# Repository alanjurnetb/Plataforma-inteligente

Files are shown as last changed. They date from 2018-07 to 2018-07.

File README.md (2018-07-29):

# Plataforma-inteligente
<h1>PLATAFORMA INTELIGENTE PARA DESARROLLO DE VEHÍCULOS MÓVILES AUTÓNOMOS</h1>

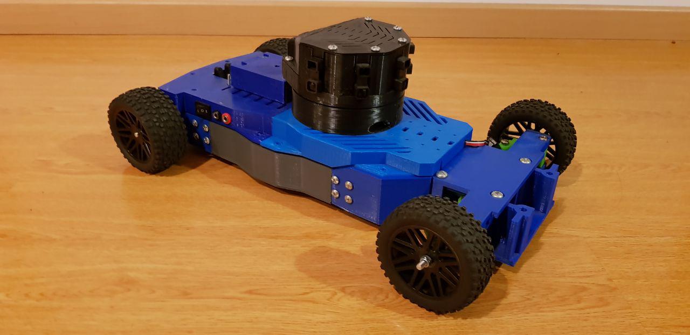
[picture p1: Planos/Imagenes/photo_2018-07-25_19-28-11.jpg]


<h2>Fabricación:</h2>
<h3>Mecánica</h3>

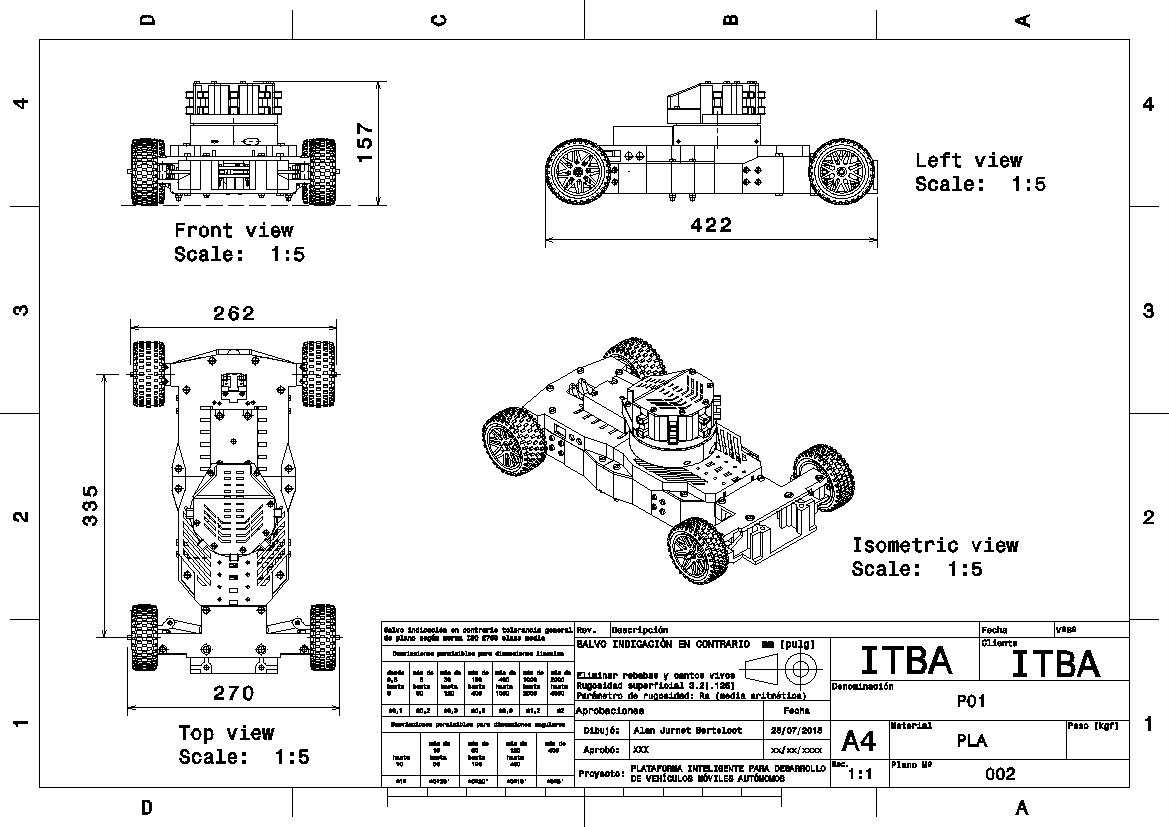
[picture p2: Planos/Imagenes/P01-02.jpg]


Todos los planos y los componentes estan detallados en la carpeta correspondiente.
A continuacion se muestra como es el ensamble y cuales son las piezas que deben utilziarse.
Todas las piezas impresas tienen una codificacion en el nombre que indica como se recomienda que sean impresas.

<b>XXXX-XXXX-I3D-L04-W20-IF50</b>

Esto indica que es una pieza impresa en 3D con capa de 0.4 mm pared de 2 mm y relleno de 50%.

<h4>Tracción</h4>

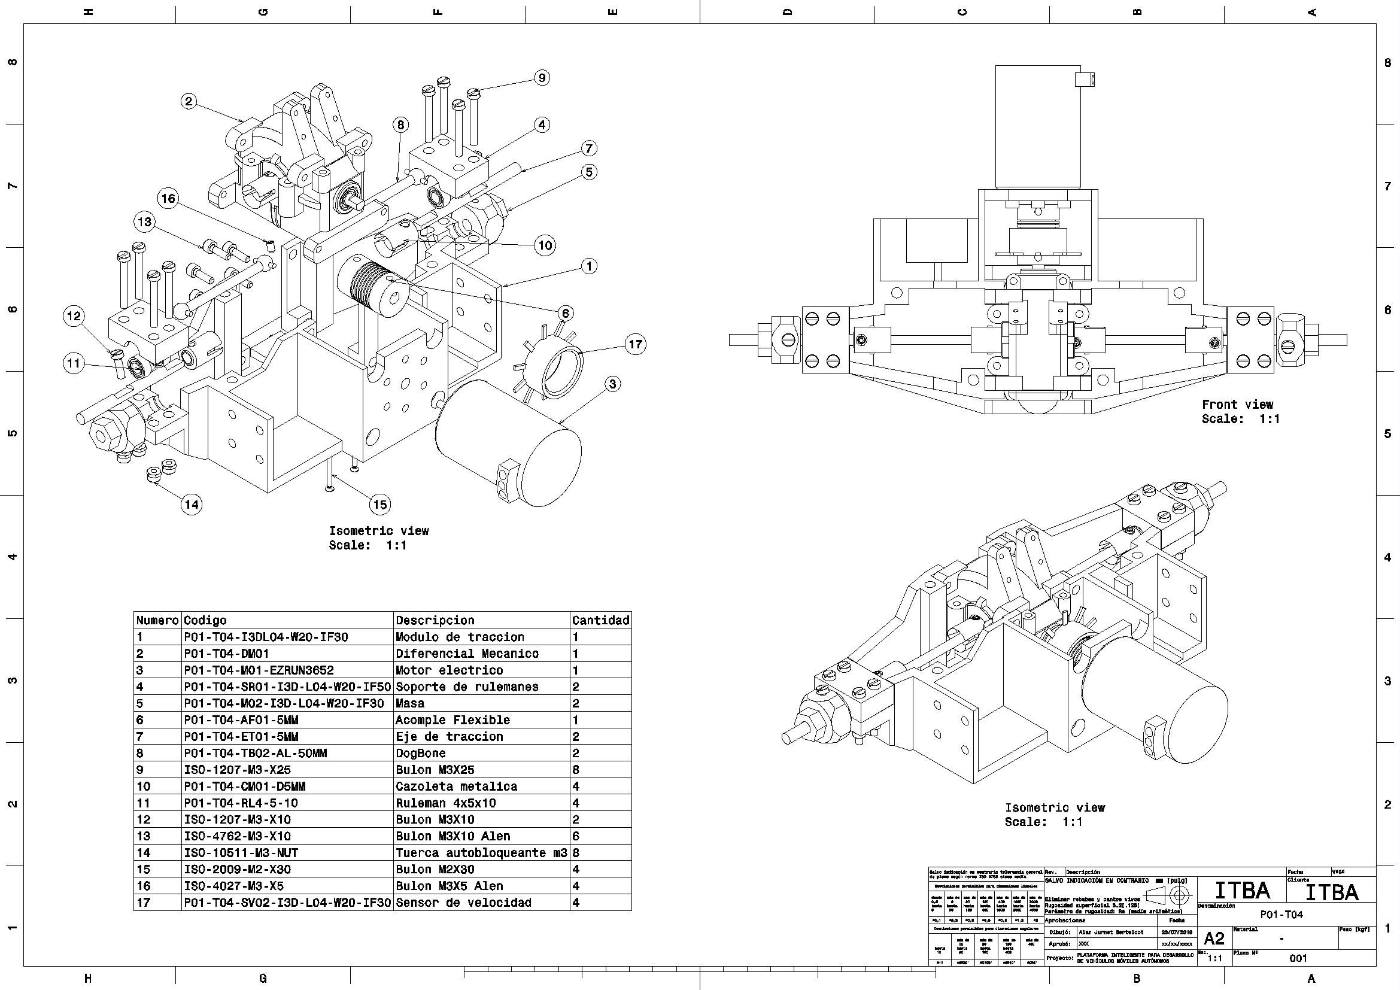
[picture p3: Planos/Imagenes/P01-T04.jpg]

<h4>Dirección</h4>

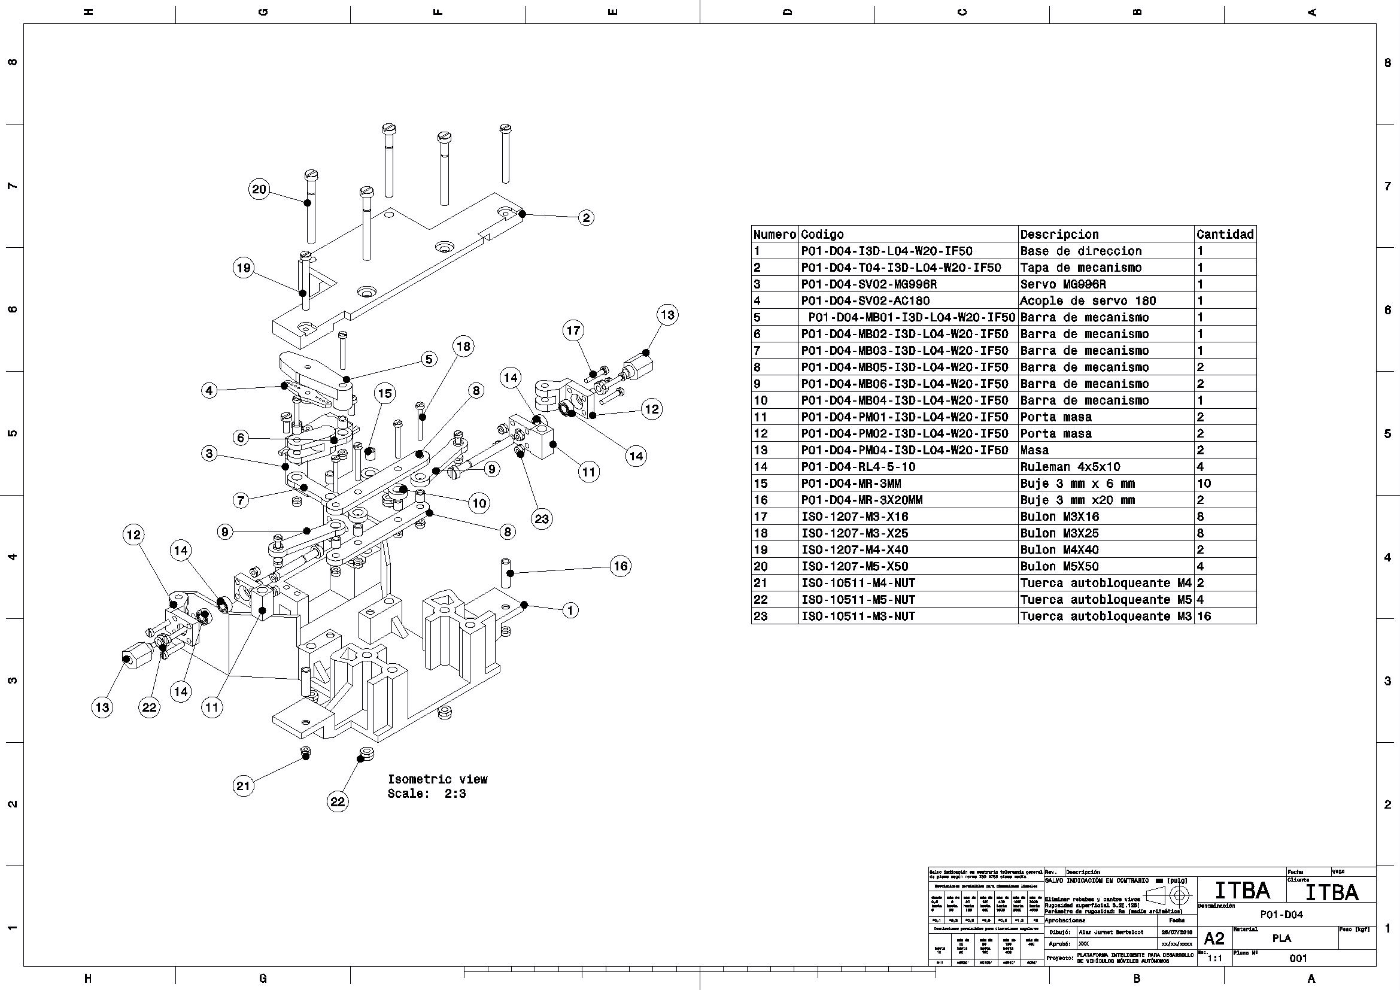
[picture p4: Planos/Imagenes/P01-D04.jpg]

<h4>Chasis</h4>

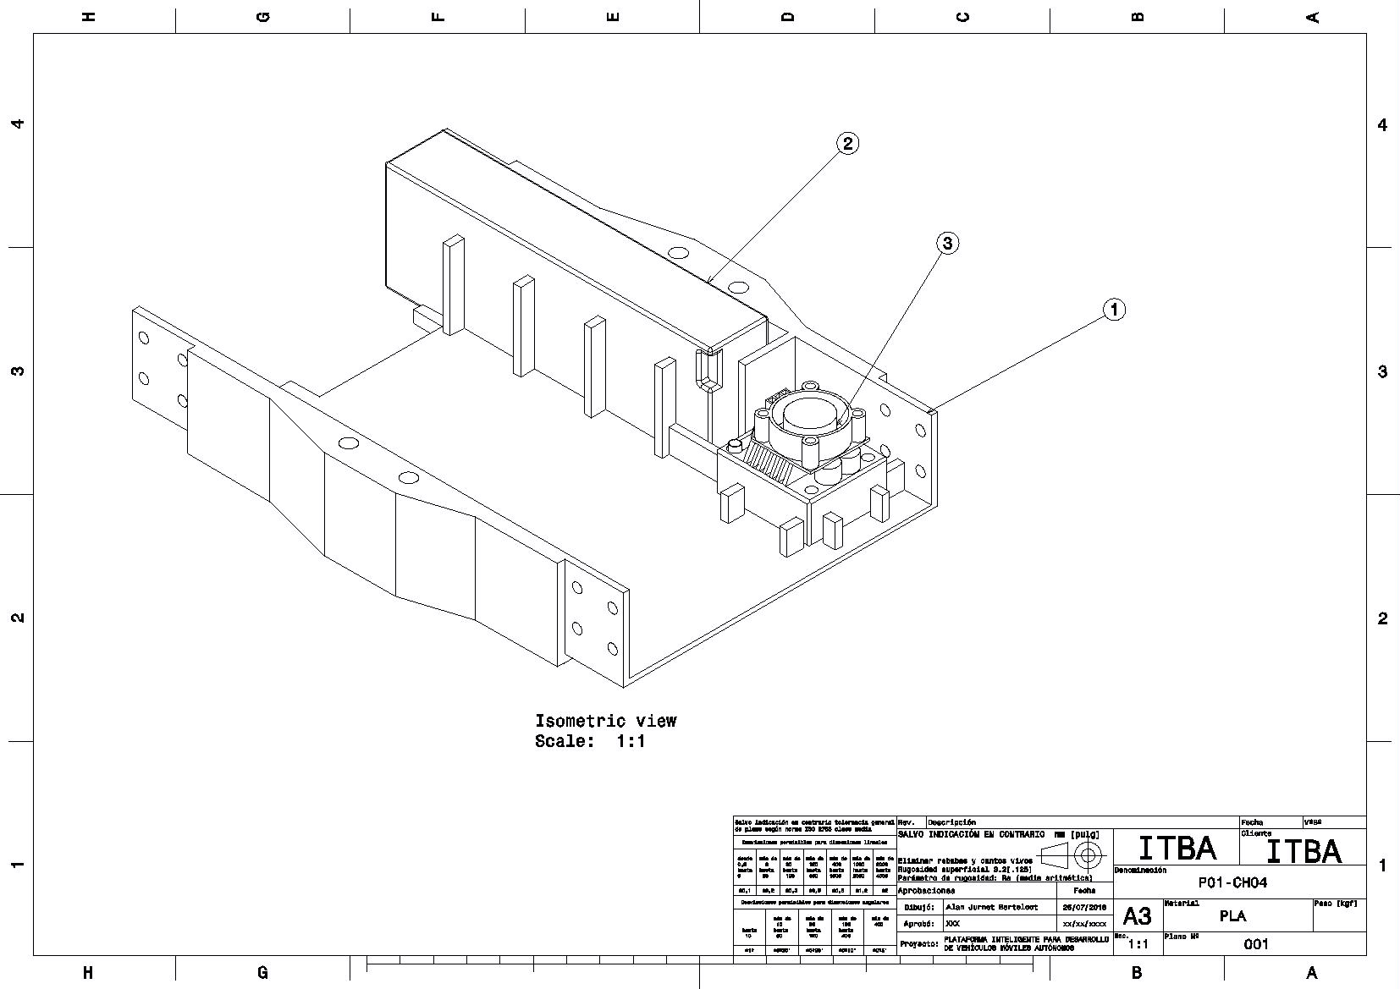
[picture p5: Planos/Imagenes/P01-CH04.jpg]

<h4>Radar</h4>

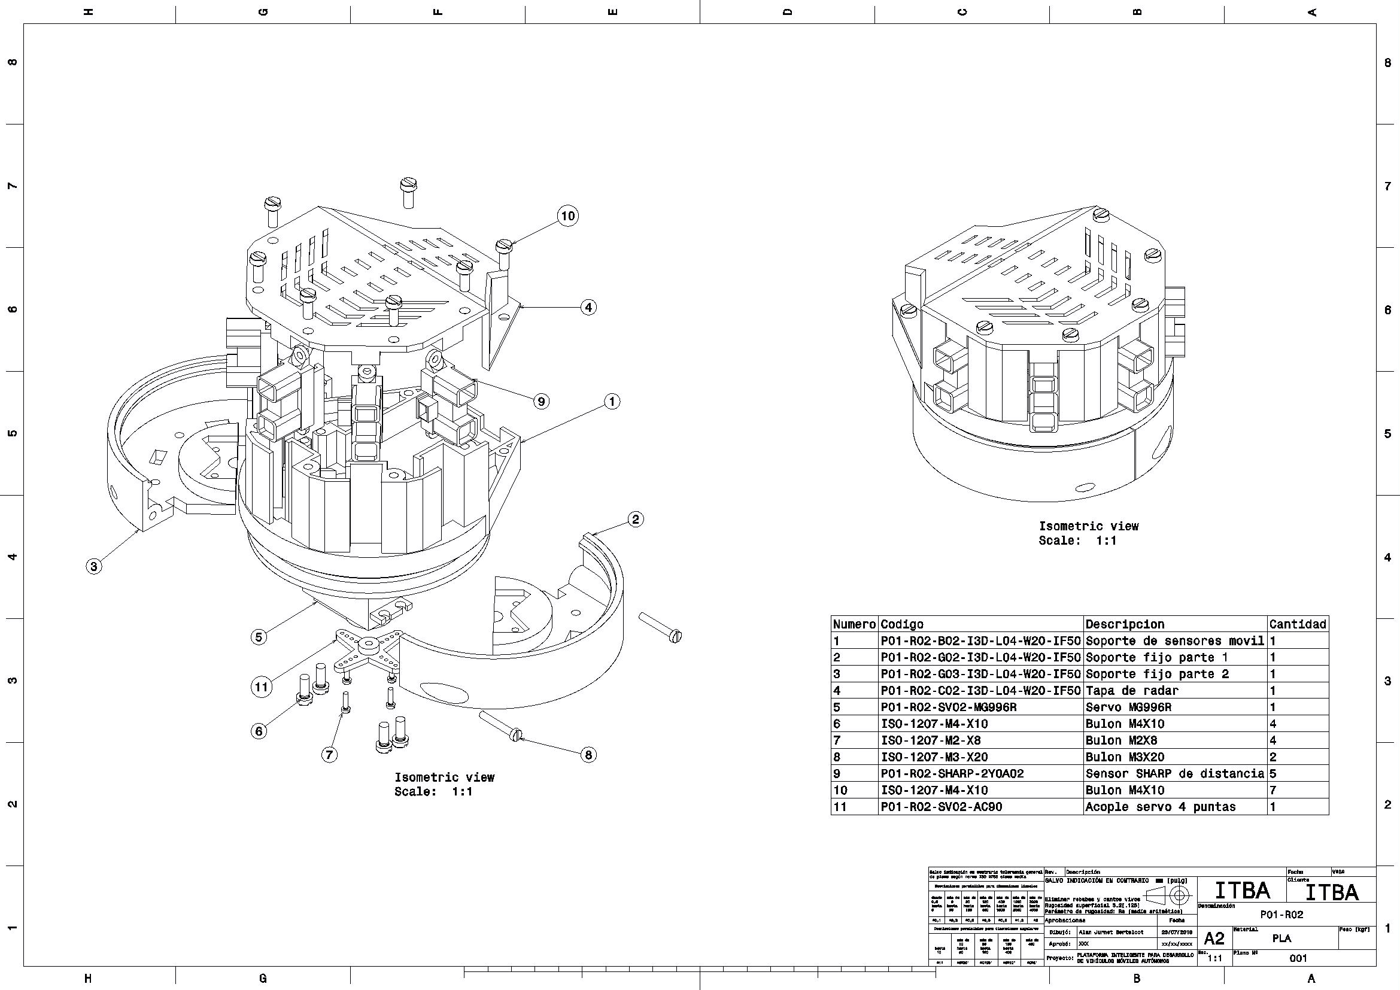
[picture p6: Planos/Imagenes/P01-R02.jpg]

<h4>Control</h4>

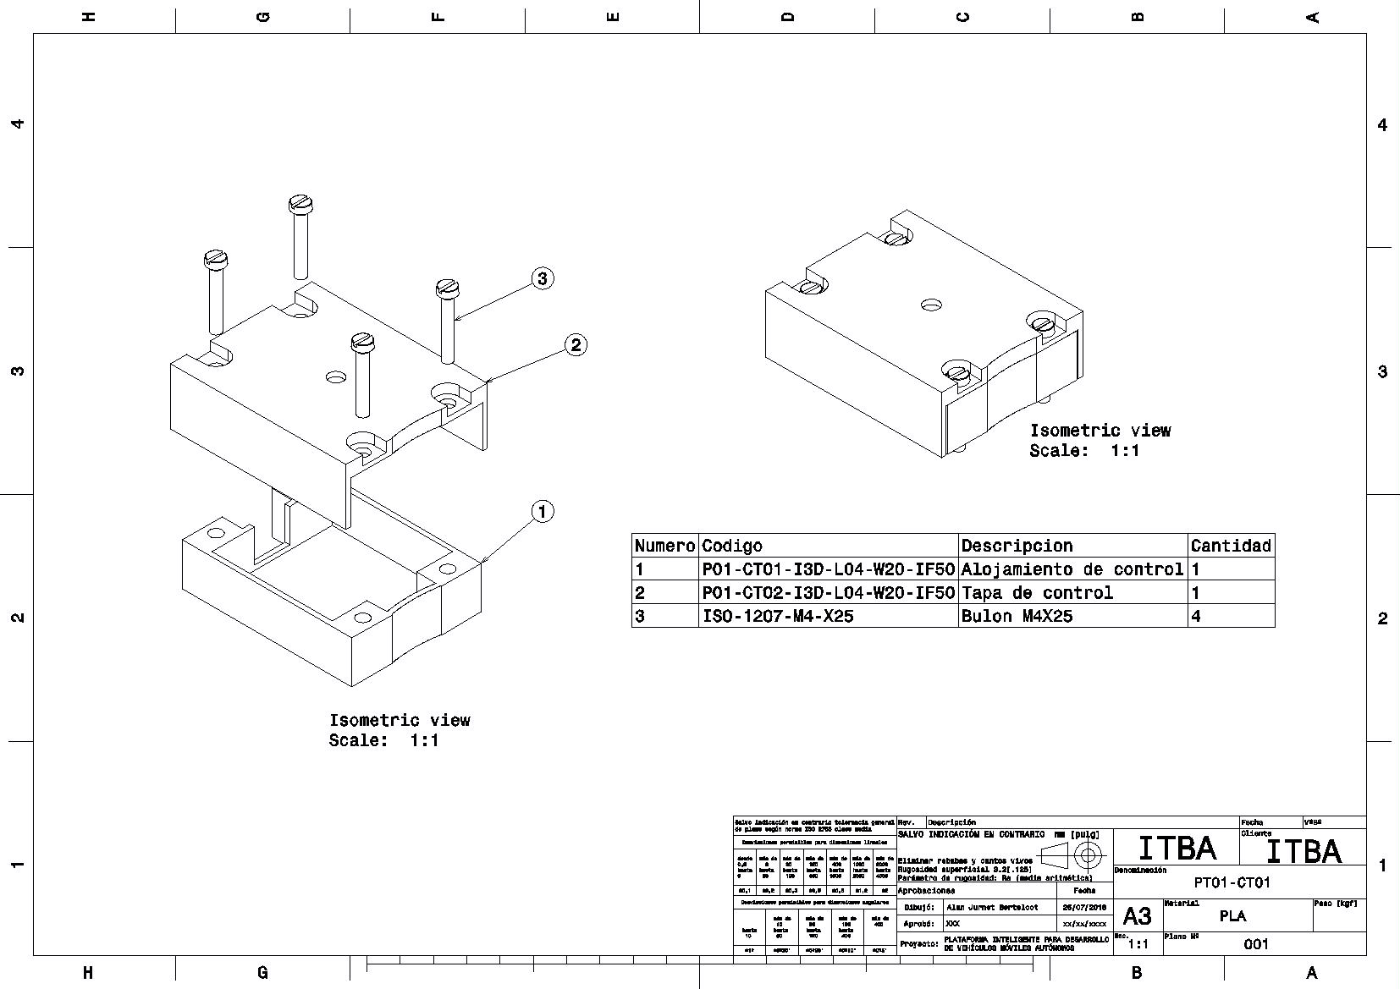
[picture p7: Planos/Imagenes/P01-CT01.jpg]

<h4>Remoto</h4>

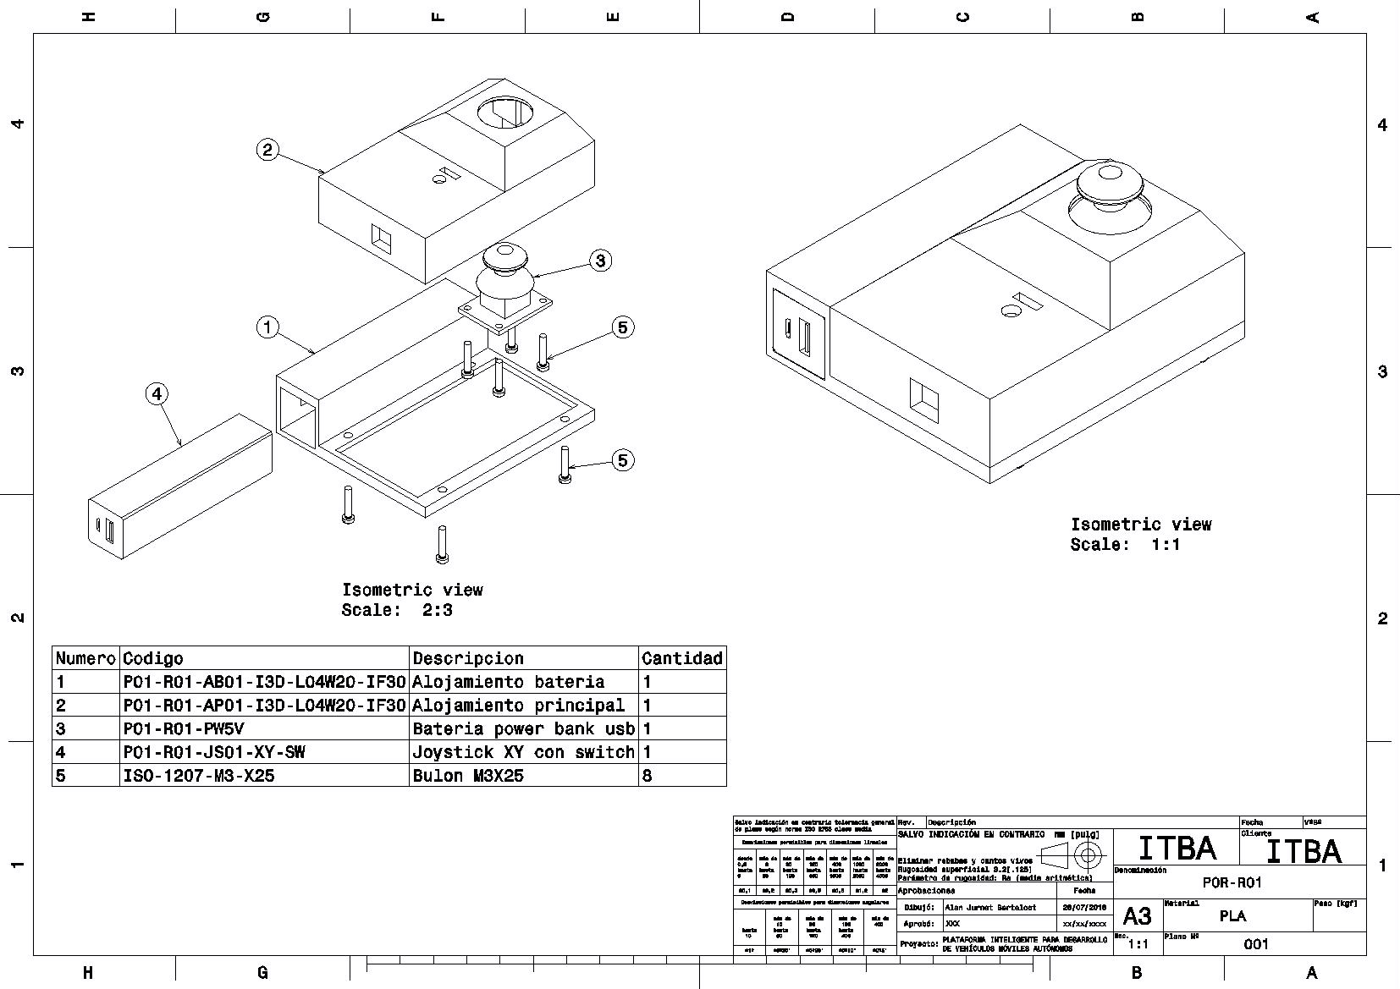
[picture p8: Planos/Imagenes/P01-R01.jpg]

<h4>Ensamble completo</h4>


<h3>Electrónica</h3>

La electrónica esta desarrollada en base a modulos comerciales y no es necesario fabricar ningun pcb. Esta versión fue fabricada utilziando placas multiperforadas y componentes básicos como conectores.

El detalle de construcción esta en la carpeta de electrónica.

<h3>Software</h3>
Todos los códigos estan realizados en Arduino y C++, se utilizaron librerias comerciales y se programaron otras. En la carpeta de Códigos se encuentra cada detalle.

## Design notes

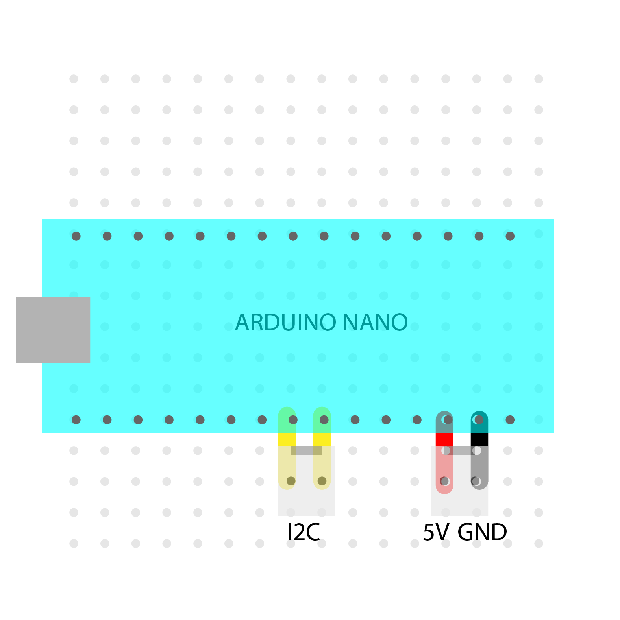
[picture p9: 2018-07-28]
Electronica/Modulo control/PCBs-04.png

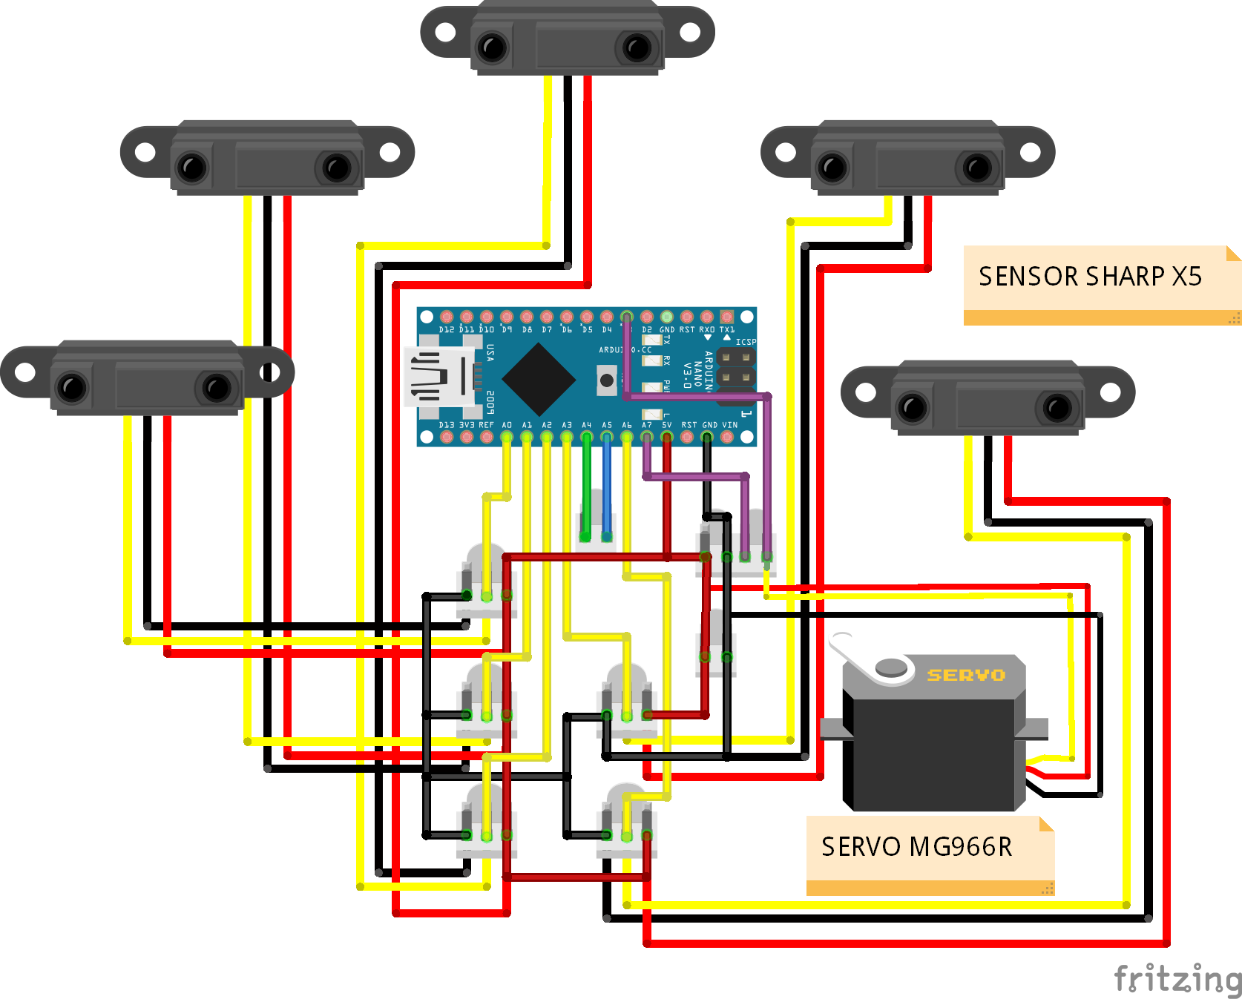
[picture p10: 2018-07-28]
Electronica/Modulo radar/Modulo radar_bb.png

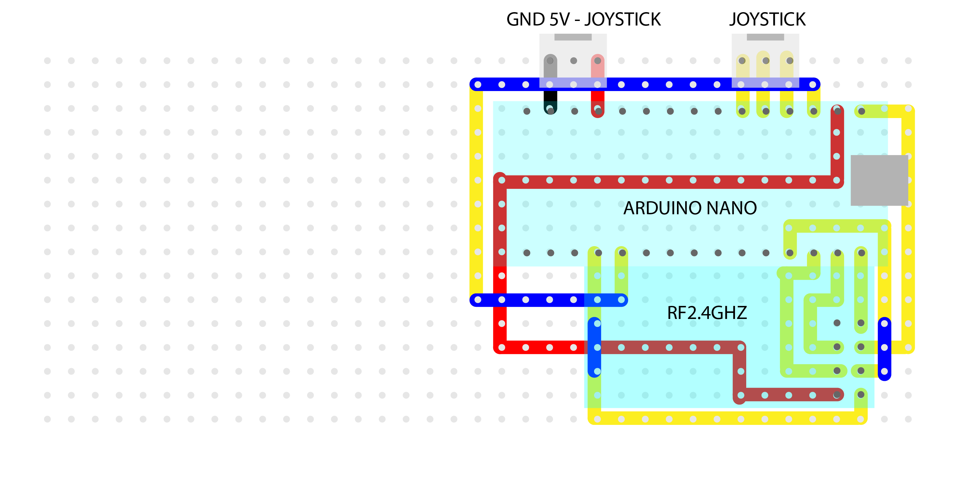
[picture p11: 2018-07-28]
Electronica/Modulo remoto/PCBs-02.png

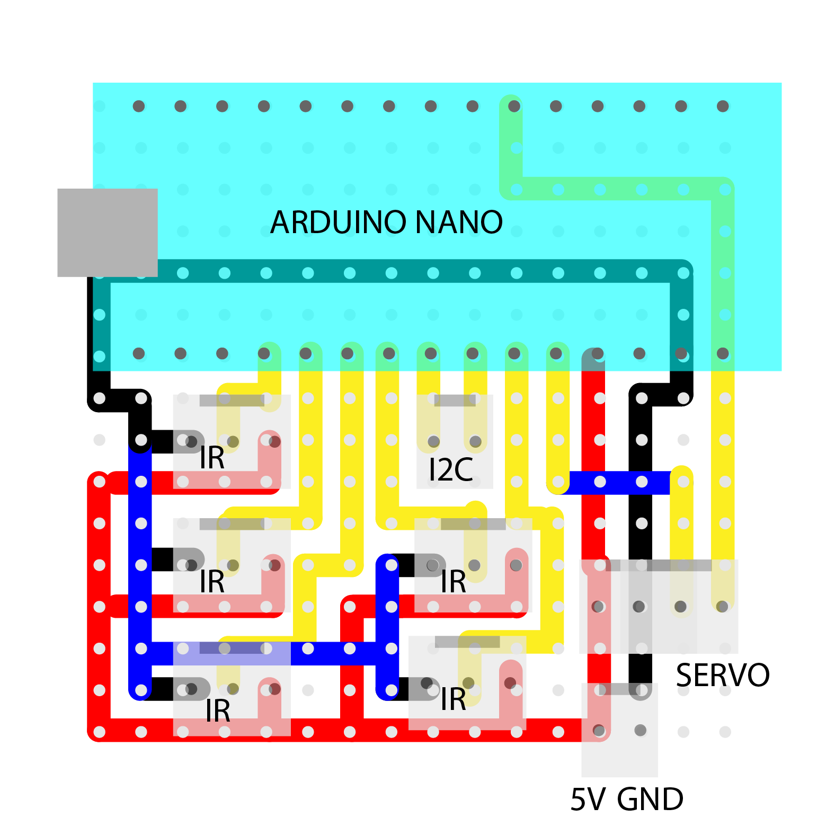
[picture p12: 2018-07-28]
Electronica/Modulo radar/PCBs-03.png

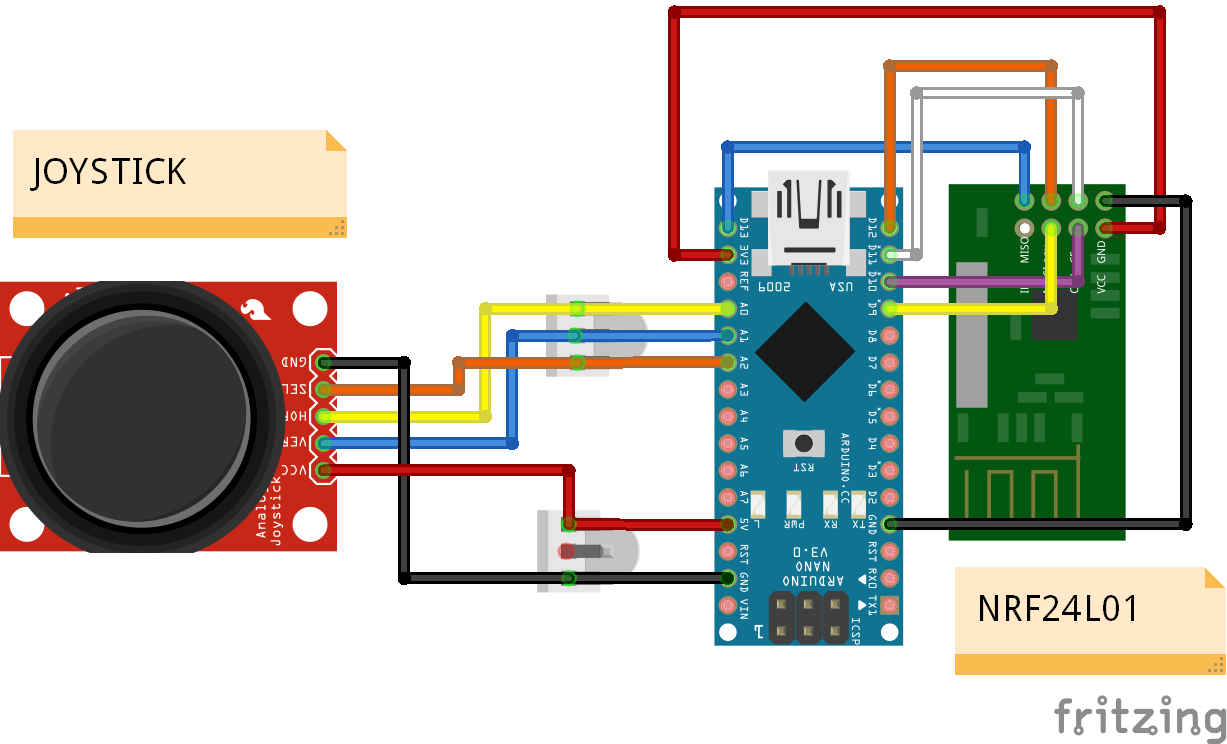
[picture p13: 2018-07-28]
Electronica/Modulo remoto/Modulo remoto_bb.png

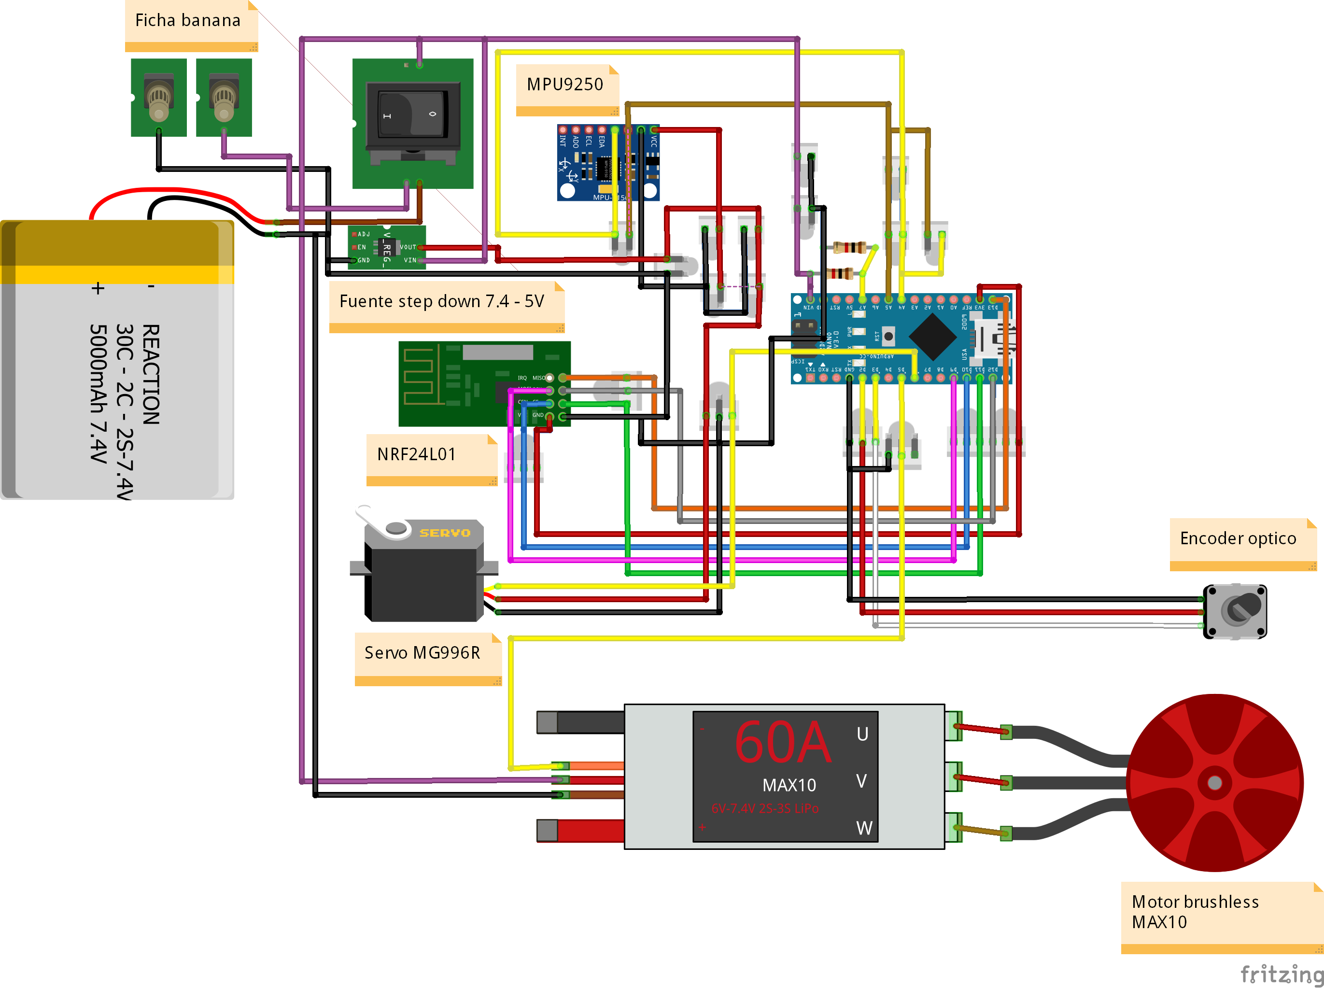
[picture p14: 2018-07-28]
Electronica/Modulo Central/Modulo central_bb.png

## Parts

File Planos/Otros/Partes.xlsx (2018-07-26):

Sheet: Sheet1
Numero | Codigo | Descripcion | Cantidad
1 | P01-T04-I3DL04-W20-IF30 | Modulo de traccion | 1
2 | P01-T04-DM01 | Diferencial Mecanico | 1
3 | P01-T04-M01-EZRUN3652 | Motor electrico | 1
4 | P01-T04-SR01-I3D-L04-W20-IF50 | Soporte de rulemanes | 2
5 | P01-T04-M02-I3D-L04-W20-IF30 | Masa | 2
6 | P01-T04-AF01-5MM | Acomple Flexible | 1
7 | P01-T04-ET01-5MM | Eje de traccion | 2
8 | P01-T04-TB02-AL-50MM | DogBone | 2
9 | ISO-1207-M3-X25 | Bulon M3X25 | 8
10 | P01-T04-CM01-D5MM | Cazoleta metalica | 4
11 | P01-T04-RL4-5-10 | Ruleman 4x5x10 | 4
12 | ISO-1207-M3-X10 | Bulon M3X10 | 2
13 | ISO-4762-M3-X10 | Bulon M3X10 Alen | 6
14 | ISO-10511-M3-NUT | Tuerca autobloqueante m3 | 8
15 | ISO-2009-M2-X30 | Bulon M2X30 | 4
16 | ISO-4027-M3-X5 | Bulon M3X5 Alen | 4

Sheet: Sheet2
Numero | Codigo | Descripcion | Cantidad
1 | P01-D04-I3D-L04-W20-IF50 | Base de direccion | 1
2 | P01-D04-T04-I3D-L04-W20-IF50 | Tapa de mecanismo | 1
3 | P01-D04-SV02-MG996R | Servo MG996R | 1
4 | P01-D04-SV02-AC180 | Acople de servo 180 | 1
5 | P01-D04-MB01-I3D-L04-W20-IF50 | Barra de mecanismo | 1
6 | P01-D04-MB02-I3D-L04-W20-IF50 | Barra de mecanismo | 1
7 | P01-D04-MB03-I3D-L04-W20-IF50 | Barra de mecanismo | 1
8 | P01-D04-MB05-I3D-L04-W20-IF50 | Barra de mecanismo | 2
9 | P01-D04-MB06-I3D-L04-W20-IF50 | Barra de mecanismo | 2
10 | P01-D04-MB04-I3D-L04-W20-IF50 | Barra de mecanismo | 1
11 | P01-D04-PM01-I3D-L04-W20-IF50 | Porta masa | 2
12 | P01-D04-PM02-I3D-L04-W20-IF50 | Porta masa | 2
13 | P01-D04-PM04-I3D-L04-W20-IF50 | Masa | 2
14 | P01-D04-RL4-5-10 | Ruleman 4x5x10 | 4
15 | P01-D04-MR-3MM | Buje 3 mm x 6 mm | 10
16 | P01-D04-MR-3X20MM | Buje 3 mm x20 mm | 2
17 | ISO-1207-M3-X16 | Bulon M3X16 | 8
18 | ISO-1207-M3-X25 | Bulon M3X25 | 8
19 | ISO-1207-M4-X40 | Bulon M4X40 | 2
20 | ISO-1207-M5-X50 | Bulon M5X50 | 4
21 | ISO-10511-M4-NUT | Tuerca autobloqueante M4 | 2
22 | ISO-10511-M5-NUT | Tuerca autobloqueante M5 | 4
23 | ISO-10511-M3-NUT | Tuerca autobloqueante M3 | 16

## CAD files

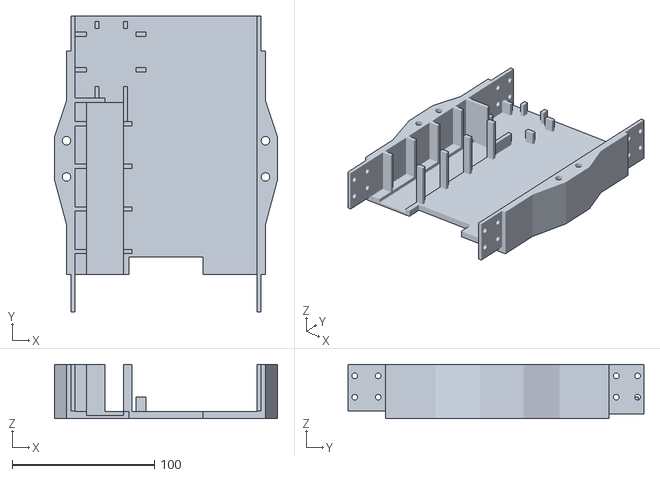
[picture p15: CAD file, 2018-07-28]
Archivos para impresion/Modulo chasis/P01-CH04-I3D-L04-W20-IF50.stl
157.0 x 208.2 x 38.0

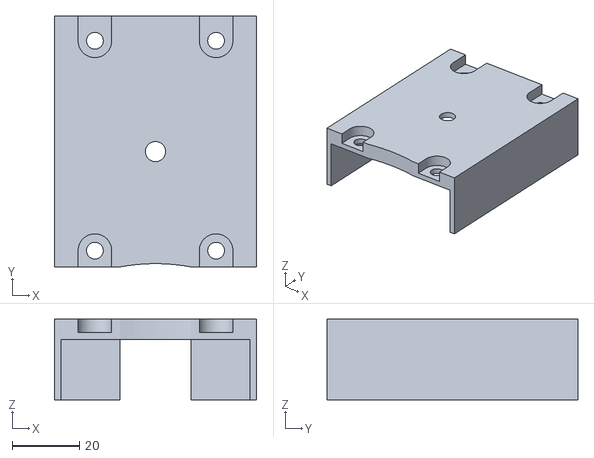
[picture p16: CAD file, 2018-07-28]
Archivos para impresion/Modulo control/P01-CT01-I3D-L04-W20-IF50.stl
60.0 x 74.5 x 24.0

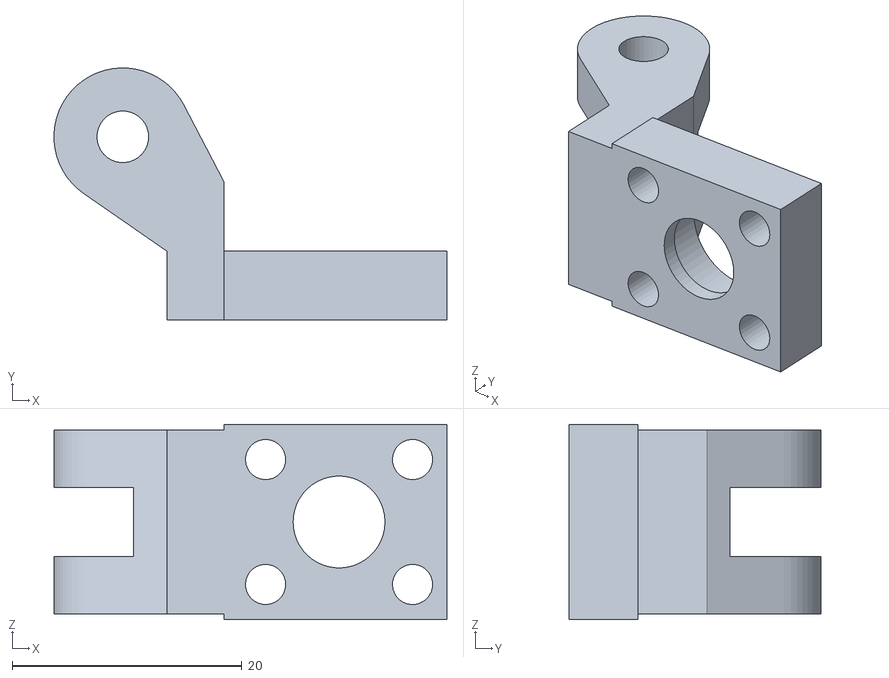
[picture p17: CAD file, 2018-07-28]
Archivos para impresion/Modulo direccion/P01-D04-PM02-I3D-L04-W20-IF50.stl
34.2 x 22.0 x 17.0

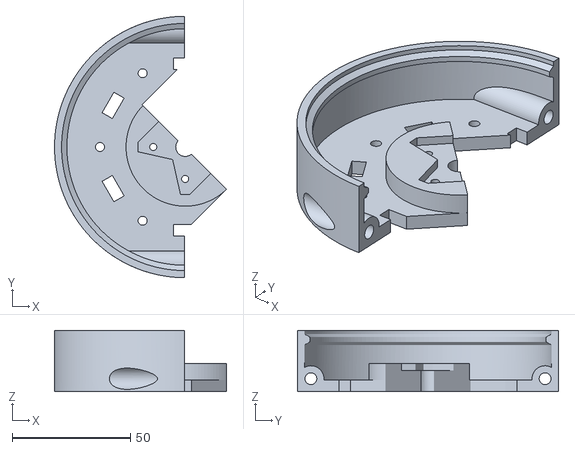
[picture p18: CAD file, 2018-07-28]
Archivos para impresion/Modulo radar/P01-R02-G02-I3D-L04-W20-IF50.stl
72.7 x 110.5 x 26.0

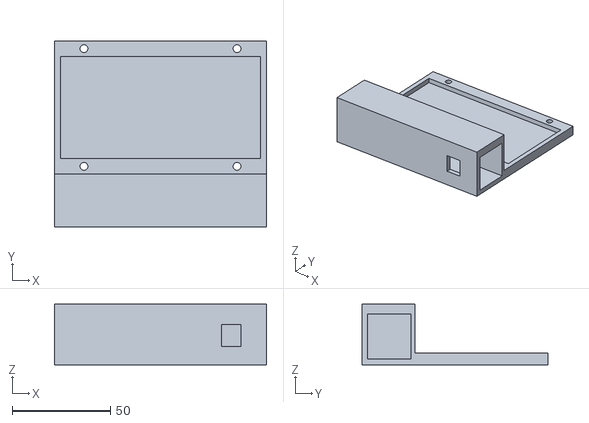
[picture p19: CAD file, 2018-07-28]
Archivos para impresion/Modulo remoto/P01-R01-AB01-I3D-L04-W20-IF30.stl
108.0 x 95.0 x 31.0

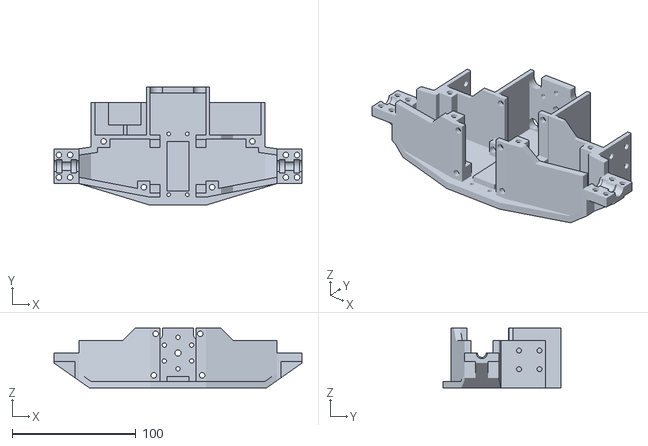
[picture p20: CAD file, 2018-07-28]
Archivos para impresion/Modulo traccion/P01-T04-I3D-L04-W20-IF30.stl
200.0 x 95.5 x 48.0

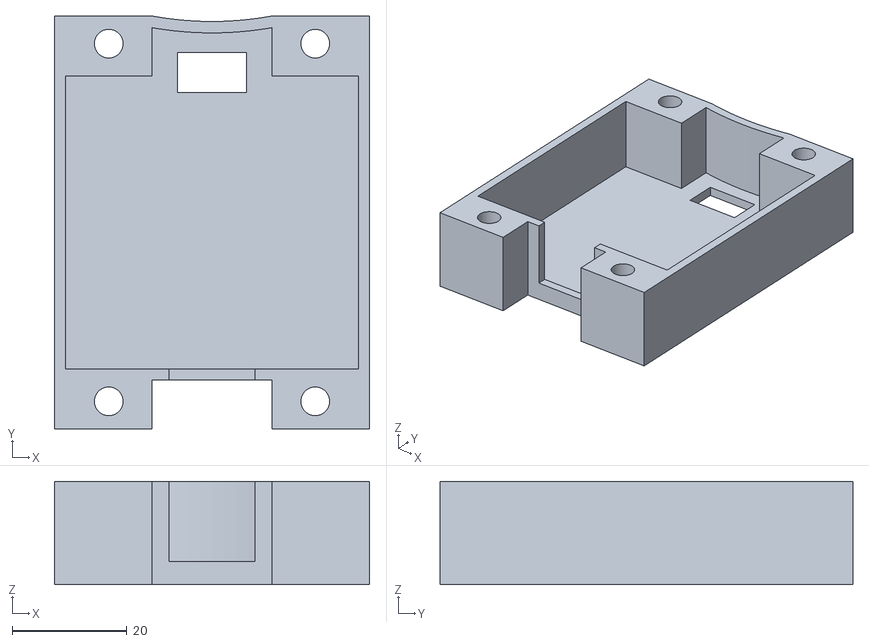
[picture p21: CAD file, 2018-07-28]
Archivos para impresion/Modulo control/P01-CT02-I3D-L04-W20-IF50.stl
55.0 x 72.0 x 18.0

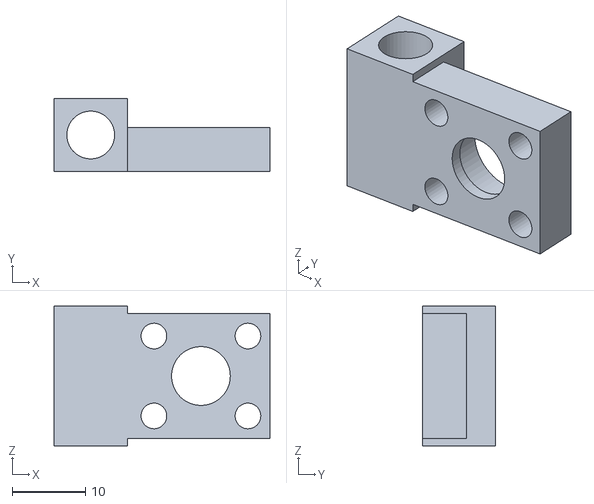
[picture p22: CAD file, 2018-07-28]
Archivos para impresion/Modulo direccion/P01-D04-PM01-I3D-L04-W20-IF50.stl
29.4 x 10.0 x 19.0

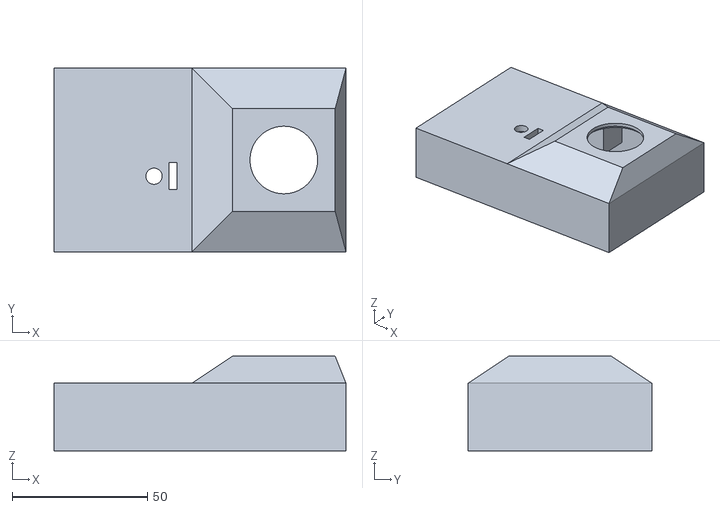
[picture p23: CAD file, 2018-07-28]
Archivos para impresion/Modulo remoto/P01-R01-AP01-I3D-L04-W20-IF30.stl
108.0 x 68.0 x 35.0

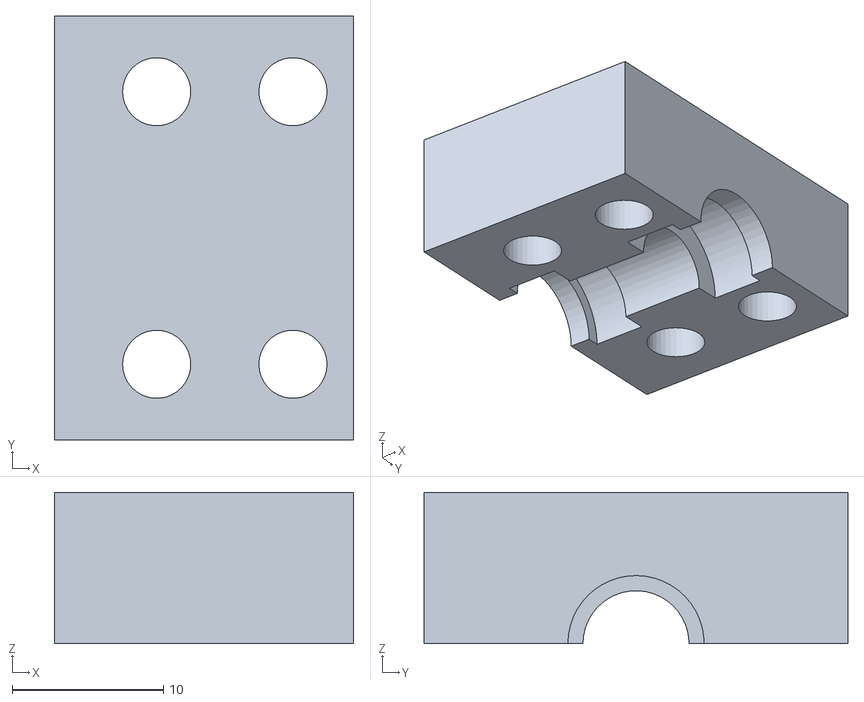
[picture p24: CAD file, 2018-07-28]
Archivos para impresion/Modulo traccion/P01-T04-SR01-I3D-L04-W20-IF50.stl
19.8 x 28.0 x 10.0

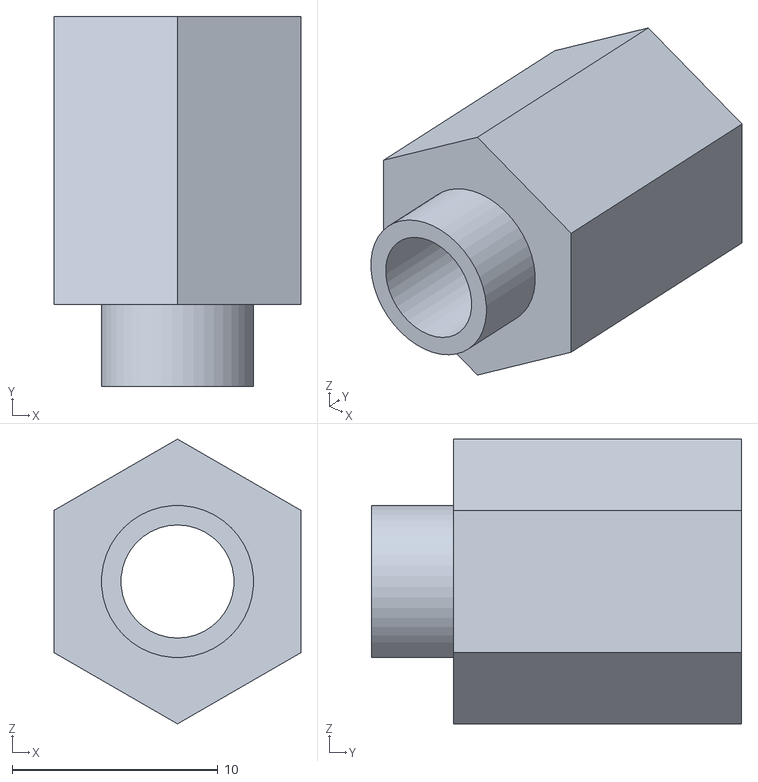
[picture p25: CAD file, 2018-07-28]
Archivos para impresion/Modulo direccion/P01-D04-PM04-I3D-L04-W20-IF50.stl
12.0 x 18.0 x 13.9

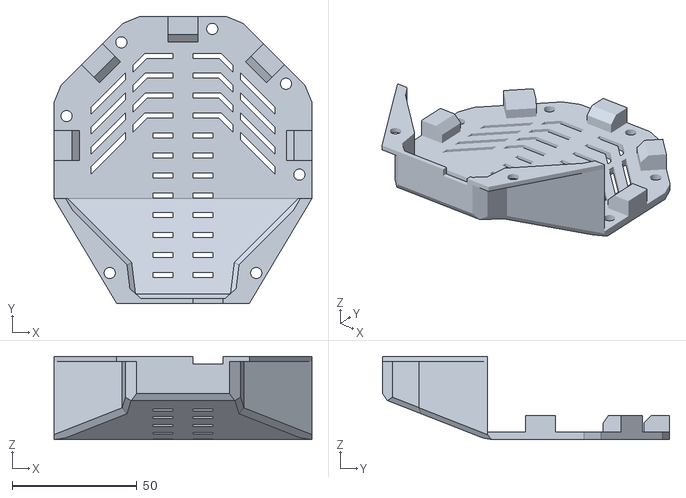
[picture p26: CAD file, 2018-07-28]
Archivos para impresion/Modulo radar/P01-R02-C02-I3D-L04-W20-IF50.stl
103.5 x 115.2 x 33.5

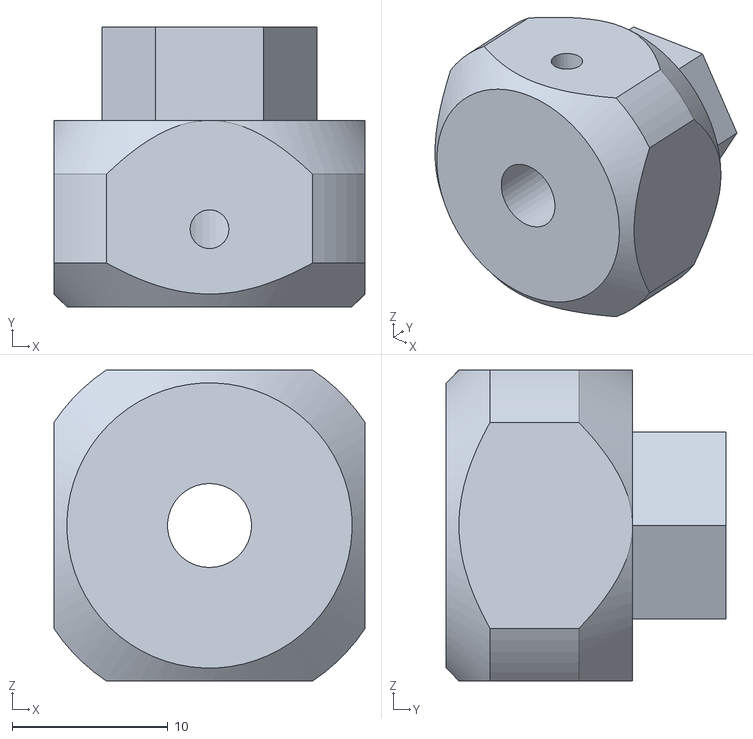
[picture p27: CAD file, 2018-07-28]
Archivos para impresion/Modulo traccion/P01-T04-M02-I3D-L04-W20-IF30.stl
20.0 x 18.0 x 20.0

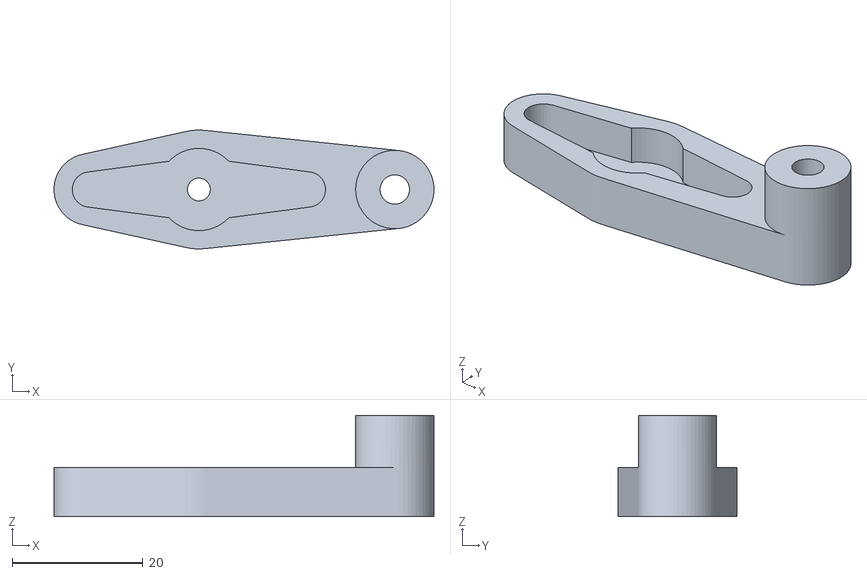
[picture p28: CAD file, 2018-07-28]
Archivos para impresion/Modulo direccion/P01-D04-MB01-I3D-L04-W20-IF50.stl
58.2 x 18.2 x 15.5

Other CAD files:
Archivos para impresion/Modulo radar/P01-R02-G03-I3D-L04-W20-IF50.stl
Archivos para impresion/Modulo radar/P01-R02-B02-I3D-L04-W20-IF50.stl
Archivos para impresion/Modulo traccion/P01-T04-SV02-I3D-L04-W20-IF30.stl
Archivos para impresion/Modulo direccion/P01-D04-MB02-I3D-L04-W20-IF50.stl
Archivos para impresion/Modulo direccion/P01-D04-I3D-L04-W20-IF50.stl
Archivos para impresion/Modulo direccion/P01-D04-MB03-I3D-L04-W20-IF50.stl
Archivos para impresion/Modulo direccion/P01-D04-MB04-I3D-L04-W20-IF50.stl
Archivos para impresion/Modulo direccion/P01-D04-MB05-I3D-L04-W20-IF50.stl
Archivos para impresion/Modulo direccion/P01-D04-MB06-I3D-L04-W20-IF50.stl
Archivos para impresion/Modulo direccion/P01-D04-T04-I3D-L04-W20-IF50.stl
Piezas editables/IS0_10511_M3_STEEL_PREVAILING_TORQUE_TYPE_HEXAGON_THIN_NUT.CATPart
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

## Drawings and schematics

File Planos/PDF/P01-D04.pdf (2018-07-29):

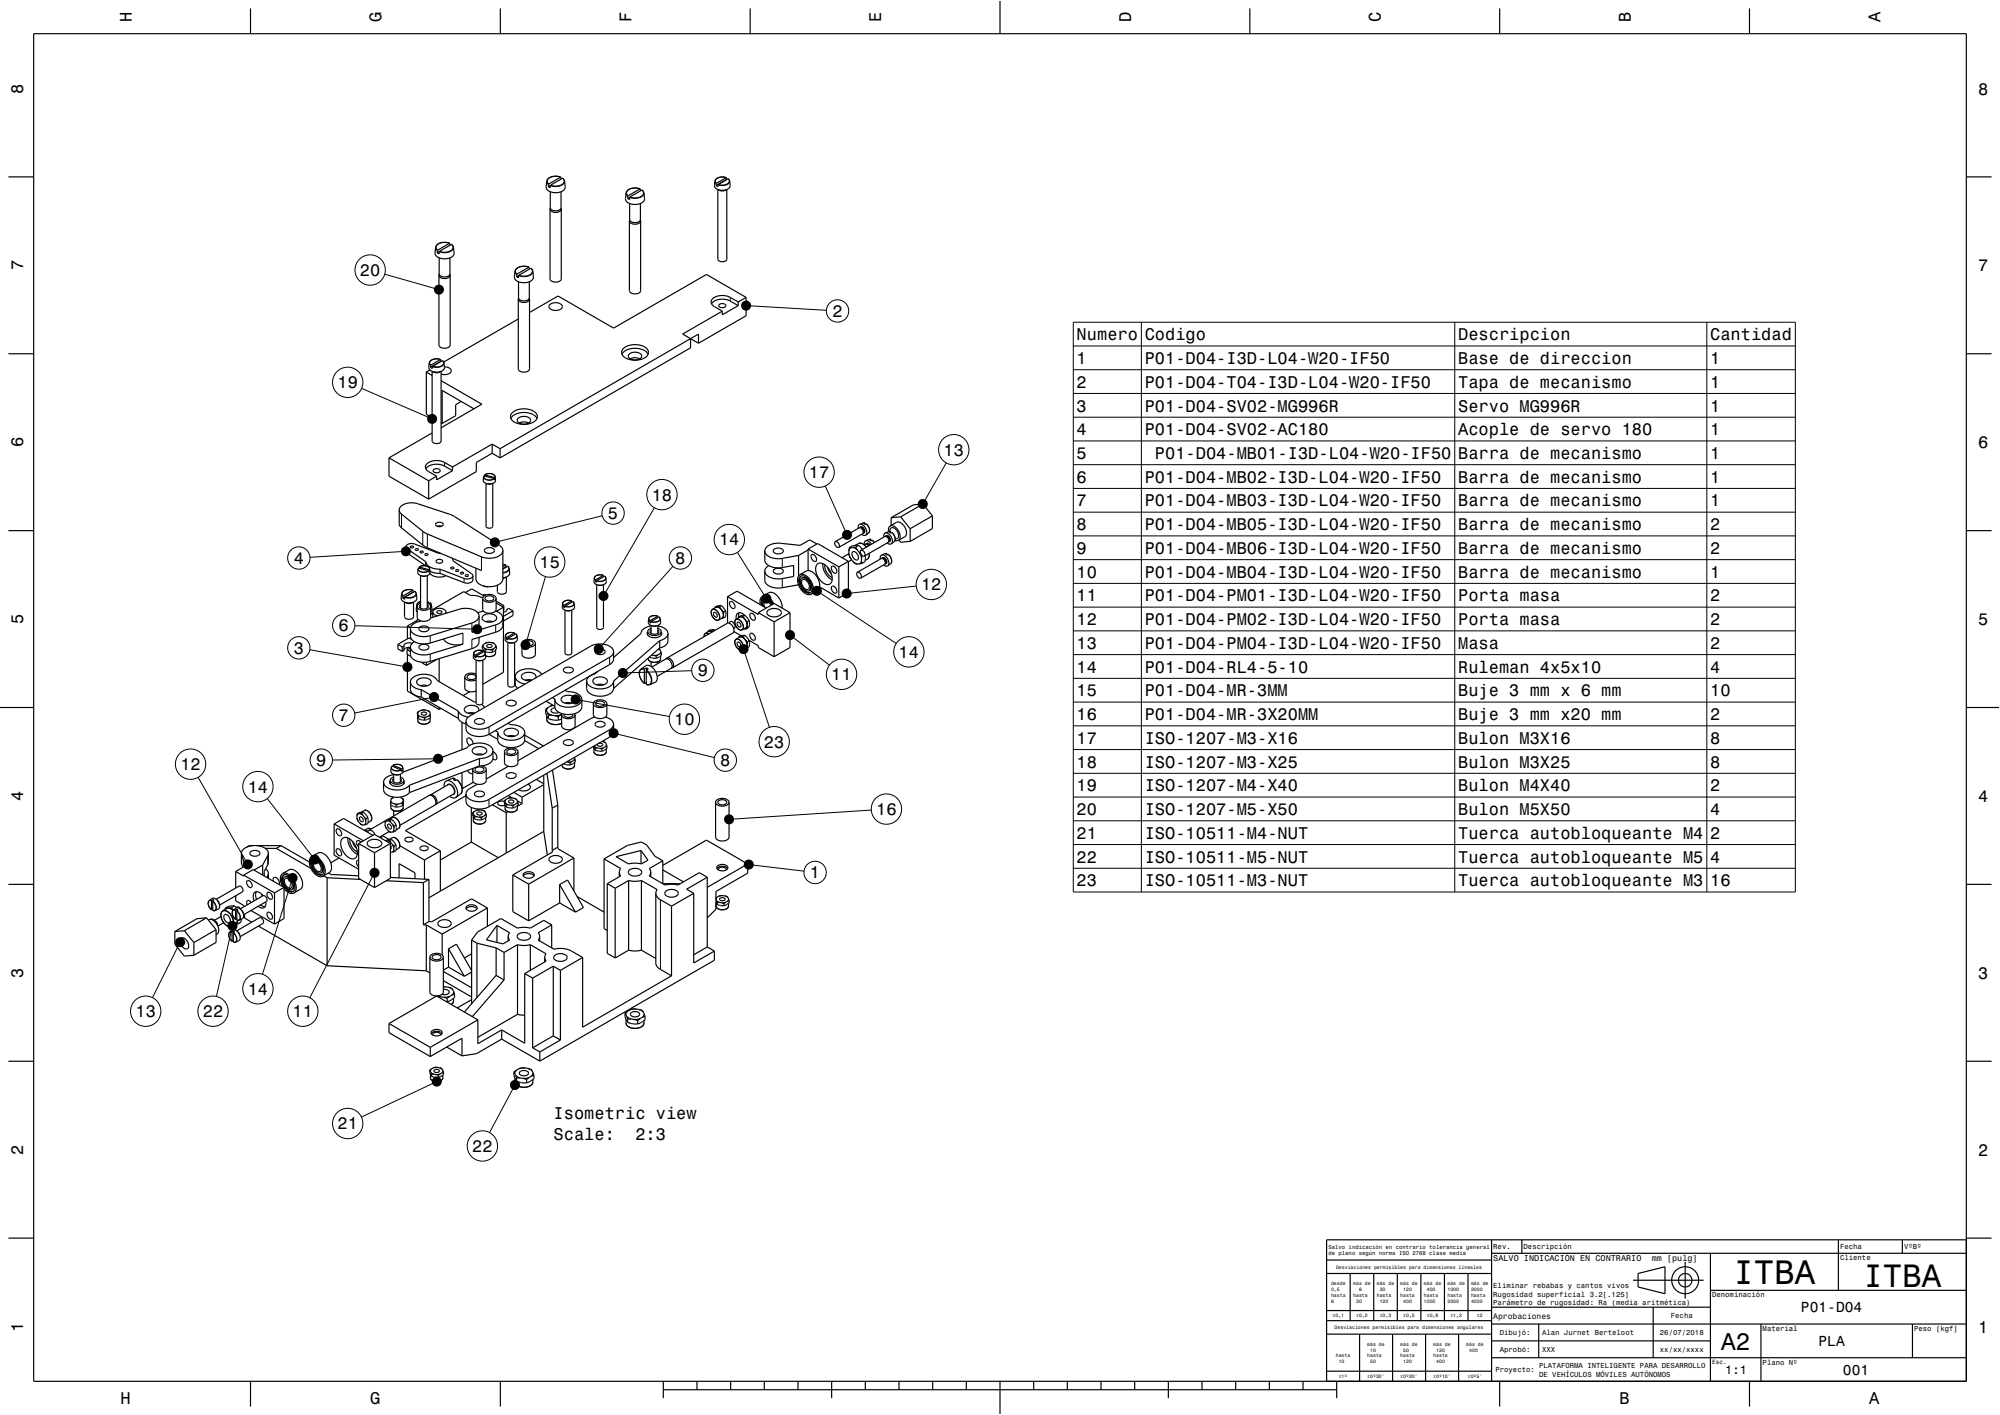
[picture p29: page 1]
Isometric view Scale: 2:3

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

Salvo indicación en contrario tolerancia general de plano según norma ISO 2768 clase media | Rev. | Descripción | Fecha | VºBº

SALVO INDICACIÓN EN CONTRARIO mm [pulg] Parámetro de rugosidad: Ra (media aritmética) | | | ITBA | Cliente ITBA

Desviaciones permisibles para dimensiones lineales

desde 0,5 hasta 6 | más de 6 hasta 30 | más de 30 hasta 120 | más de 120 hasta 400 | más de 400 hasta 1000 | más de 1000 hasta 2000 | más de 2000 hasta 4000

Eliminar rebabas y cantos vivos
Rugosidad superficial 3.2[.125]

Aprobaciones | Fecha
Dibujó: | Alan Jurnet Berteloot | 26/07/2018 | A2 | Material PLA | Peso [kgf]

Desviaciones permisibles para dimensiones angulares

hasta 10 | más de 10 hasta 50 | más de 50 hasta 120 | más de 120 hasta 400 | más de 400

Aprobó: | XXX | xx/xx/xxxx
PLATAFORMA INTELIGENTE PARA DESARROLLO Proyecto: DE VEHÍCULOS MÓVILES AUTÓNOMOS | | | Esc. 1:1 | Plano Nº 001

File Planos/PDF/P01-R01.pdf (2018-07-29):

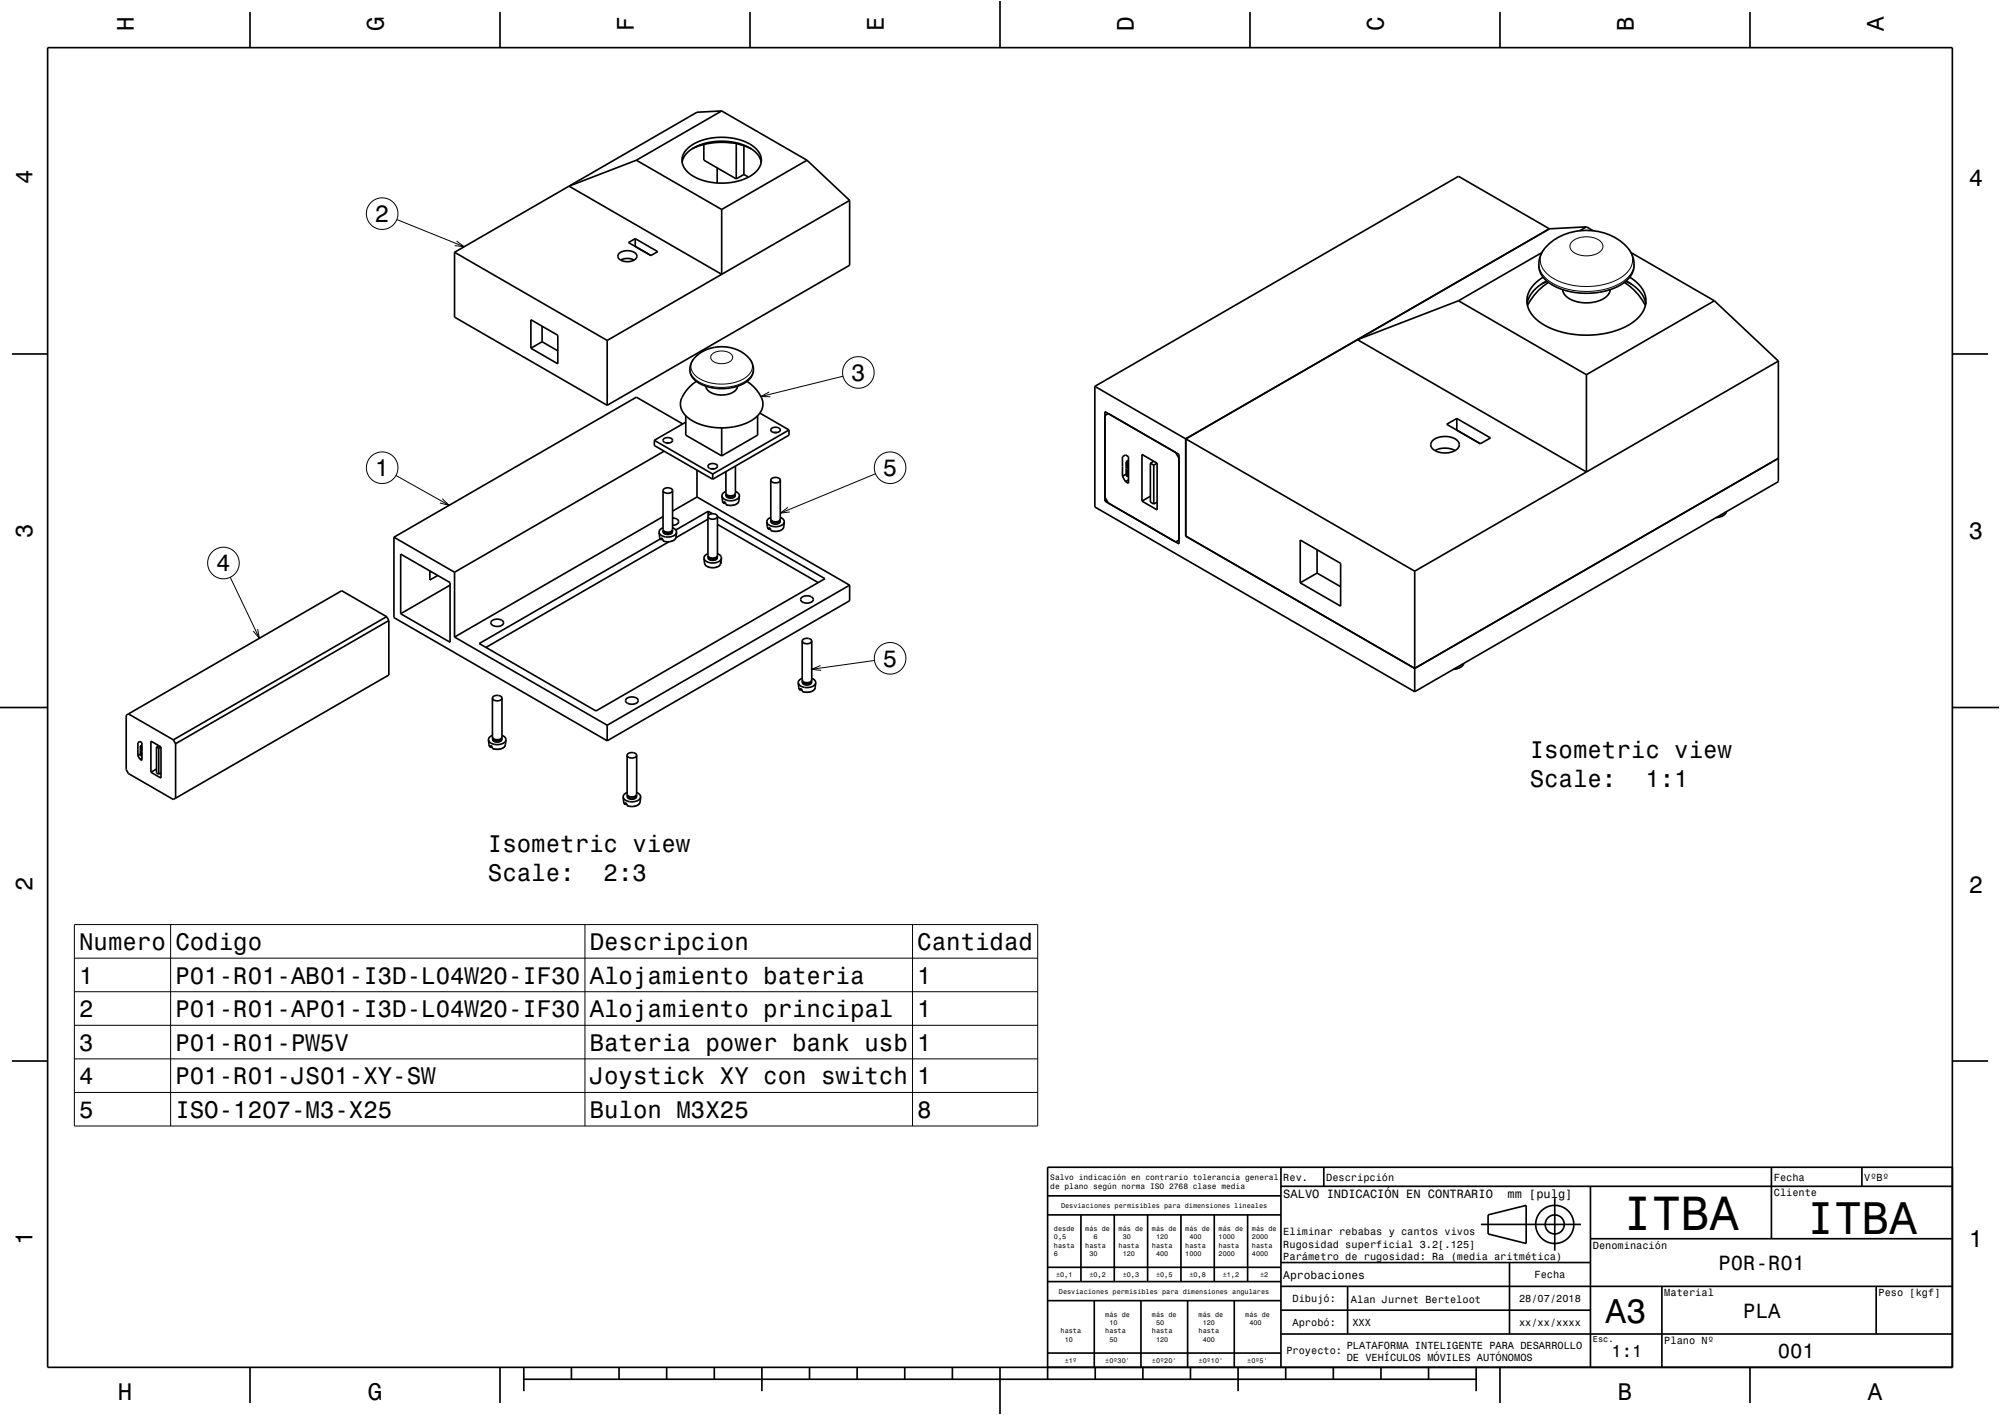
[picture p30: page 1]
Isometric view Scale: 1:1; Isometric view Scale: 2:3

Numero | Codigo | Descripcion | Cantidad
1 | P01-R01-AB01-I3D-L04W20-IF30 | Alojamiento bateria | 1
2 | P01-R01-AP01-I3D-L04W20-IF30 | Alojamiento principal | 1
3 | P01-R01-PW5V | Bateria power bank usb | 1
4 | P01-R01-JS01-XY-SW | Joystick XY con switch | 1
5 | ISO-1207-M3-X25 | Bulon M3X25 | 8

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

SALVO INDICACIÓN EN CONTRARIO mm [pulg] Parámetro de rugosidad: Ra (media aritmética) | | | ITBA | Cliente ITBA

Desviaciones permisibles para dimensiones lineales

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

Eliminar rebabas y cantos vivos
Rugosidad superficial 3.2[.125]

±0,1 | ±0,2 | ±0,3 | ±0,5 | ±0,8 | ±1,2 | ±2
Desviaciones permisibles para dimensiones angulares | Dibujó: | Alan Jurnet Berteloot | 28/07/2018 | A3 | Material PLA | Peso [kgf]

Aprobaciones | Fecha

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

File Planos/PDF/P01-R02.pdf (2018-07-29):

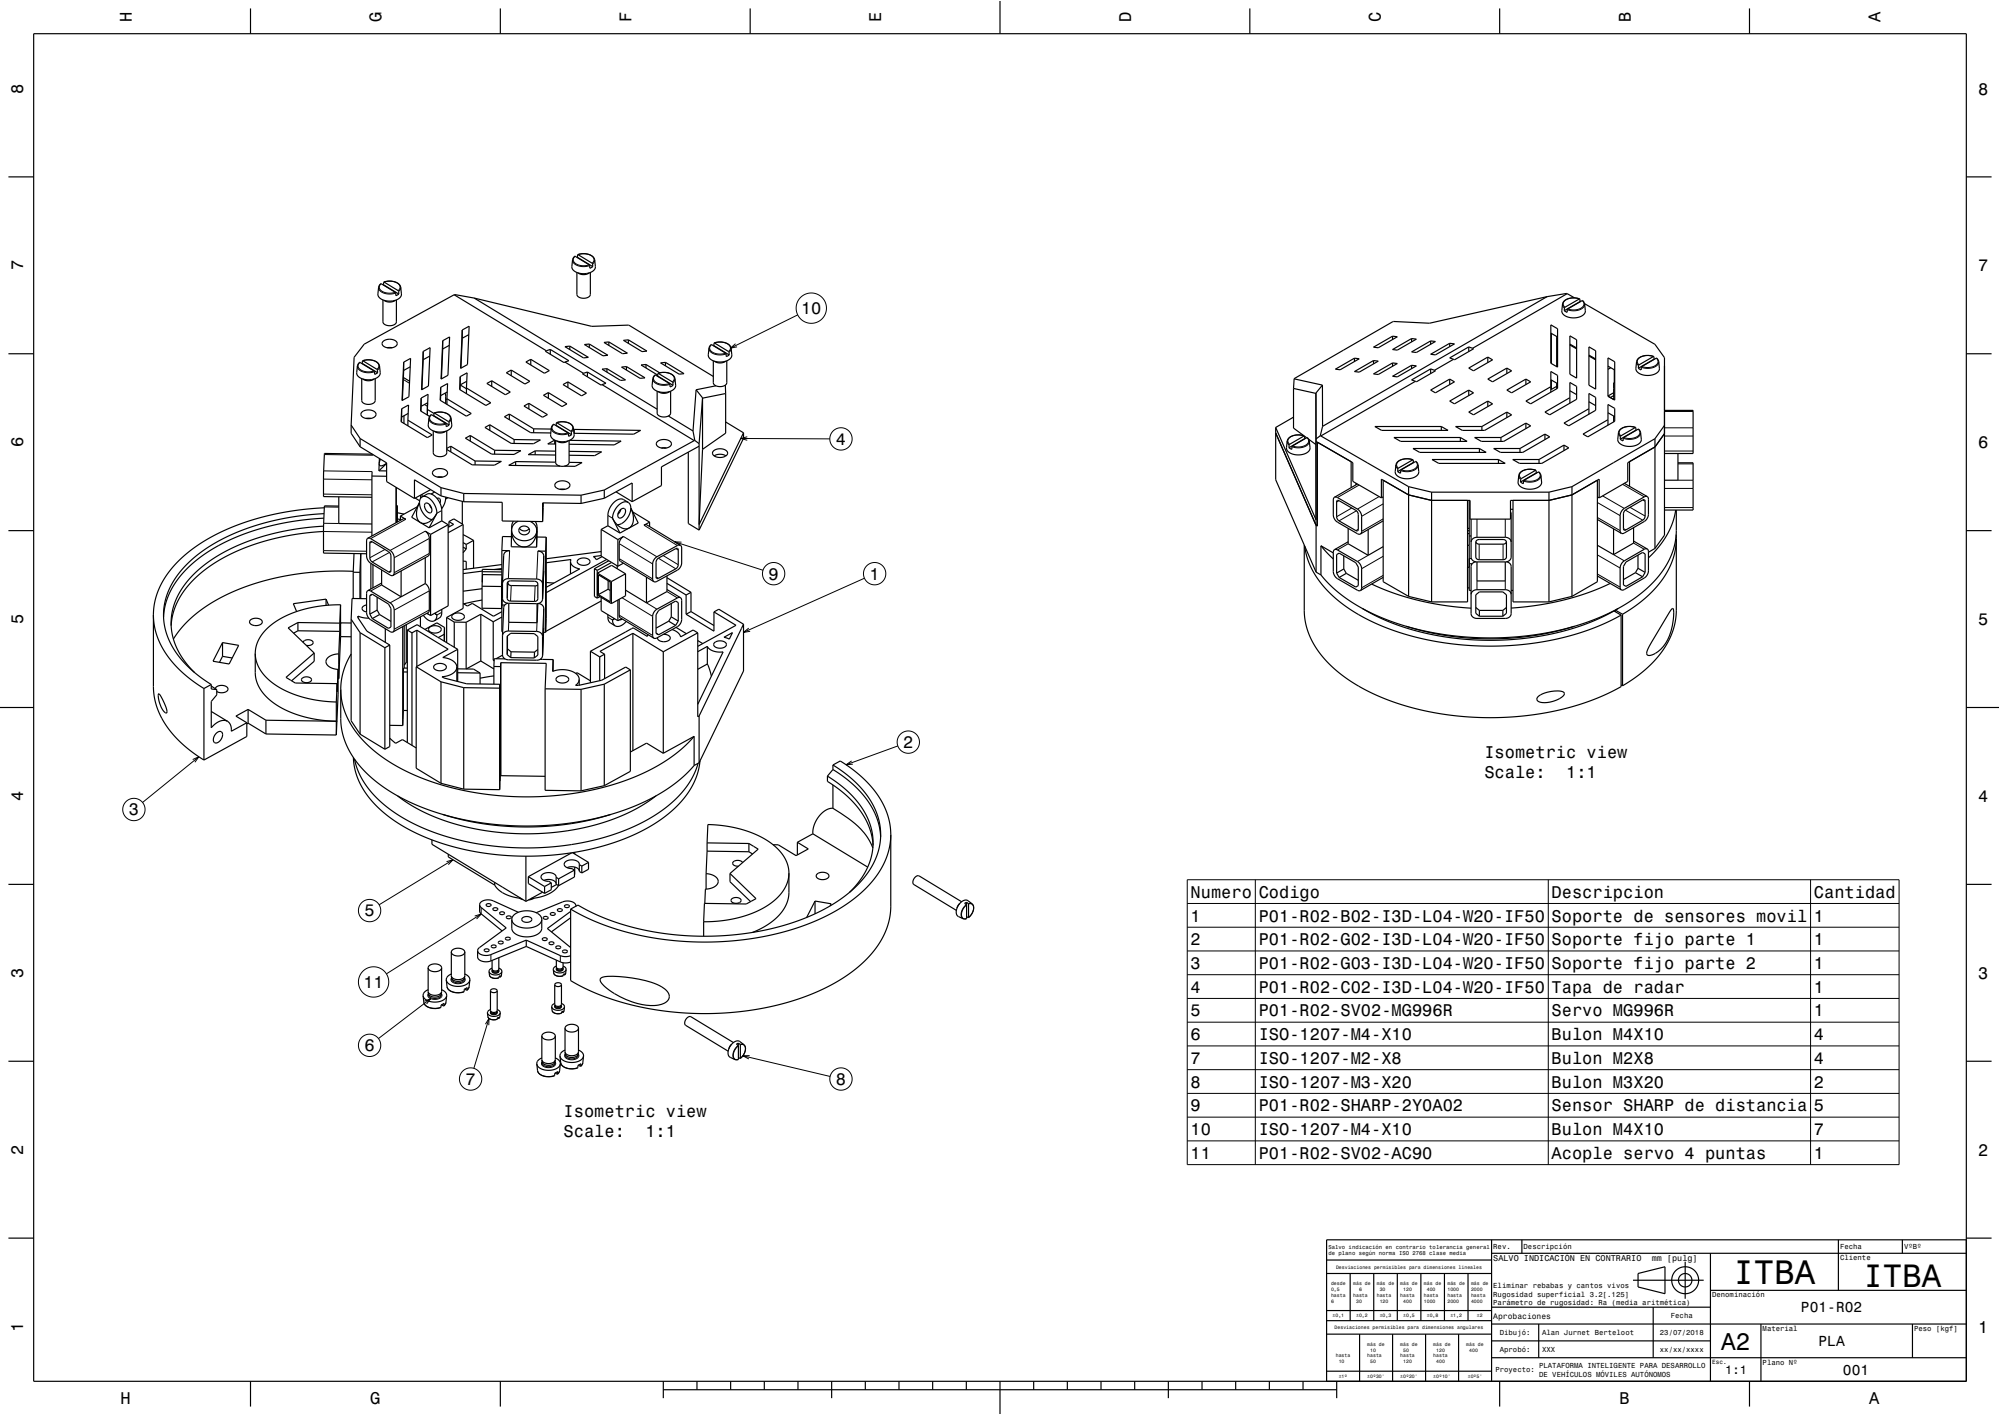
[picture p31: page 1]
Isometric view Scale: 1:1

Numero | Codigo | Descripcion | Cantidad
1 | P01-R02-B02-I3D-L04-W20-IF50 | Soporte de sensores movil | 1
2 | P01-R02-G02-I3D-L04-W20-IF50 | Soporte fijo parte 1 | 1
3 | P01-R02-G03-I3D-L04-W20-IF50 | Soporte fijo parte 2 | 1
4 | P01-R02-C02-I3D-L04-W20-IF50 | Tapa de radar | 1
5 | P01-R02-SV02-MG996R | Servo MG996R | 1
6 | ISO-1207-M4-X10 | Bulon M4X10 | 4
7 | ISO-1207-M2-X8 | Bulon M2X8 | 4
8 | ISO-1207-M3-X20 | Bulon M3X20 | 2
9 | P01-R02-SHARP-2Y0A02 | Sensor SHARP de distancia | 5
10 | ISO-1207-M4-X10 | Bulon M4X10 | 7
11 | P01-R02-SV02-AC90 | Acople servo 4 puntas | 1

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

SALVO INDICACIÓN EN CONTRARIO mm [pulg] Parámetro de rugosidad: Ra (media aritmética) | | | ITBA | Cliente ITBA

Desviaciones permisibles para dimensiones lineales

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

Eliminar rebabas y cantos vivos
Rugosidad superficial 3.2[.125]

Aprobaciones | Fecha
Dibujó: | Alan Jurnet Berteloot | 23/07/2018 | A2 | Material PLA | Peso [kgf]

Desviaciones permisibles para dimensiones angulares

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

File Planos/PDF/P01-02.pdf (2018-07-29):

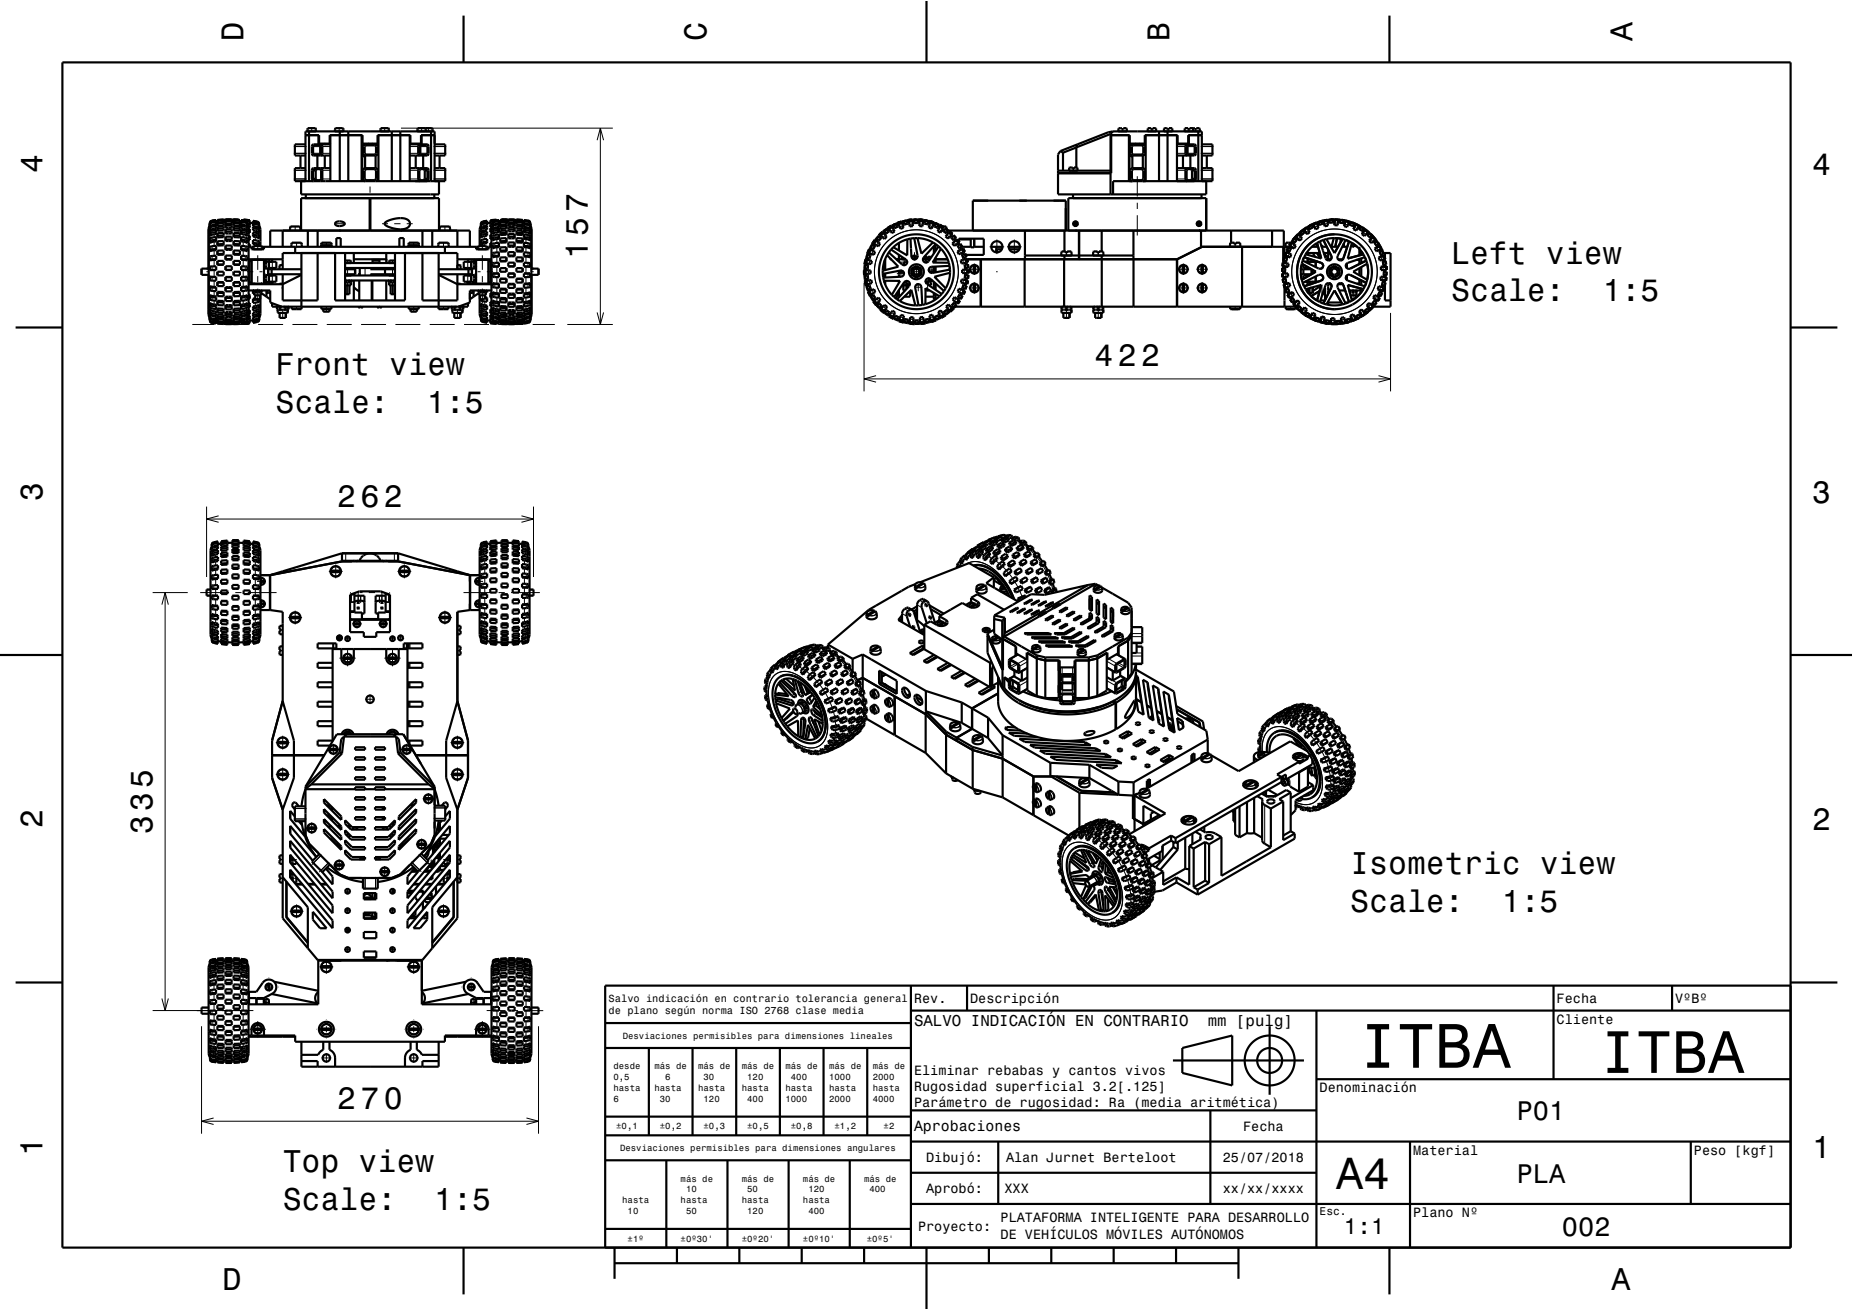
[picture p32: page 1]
Peso [kgf]; Plano Nº; más de; Front view Scale: 1:5; Left view Scale: 1:5; Top view Scale: 1:5; Isometric view Scale: 1:5

Salvo indicación en contrario tolerancia general
de plano según norma ISO 2768 clase media

Rev.
SALVO INDICACIÓN EN CONTRARIO mm [pulg]

Desviaciones permisibles para dimensiones lineales

más de
Eliminar rebabas y cantos vivos
Rugosidad superficial 3.2[.125]
Parámetro de rugosidad: Ra (media aritmética)
Aprobaciones

Desviaciones permisibles para dimensiones angulares

Alan Jurnet Berteloot
XXX
PLATAFORMA INTELIGENTE PARA DESARROLLO
DE VEHÍCULOS MÓVILES AUTÓNOMOS

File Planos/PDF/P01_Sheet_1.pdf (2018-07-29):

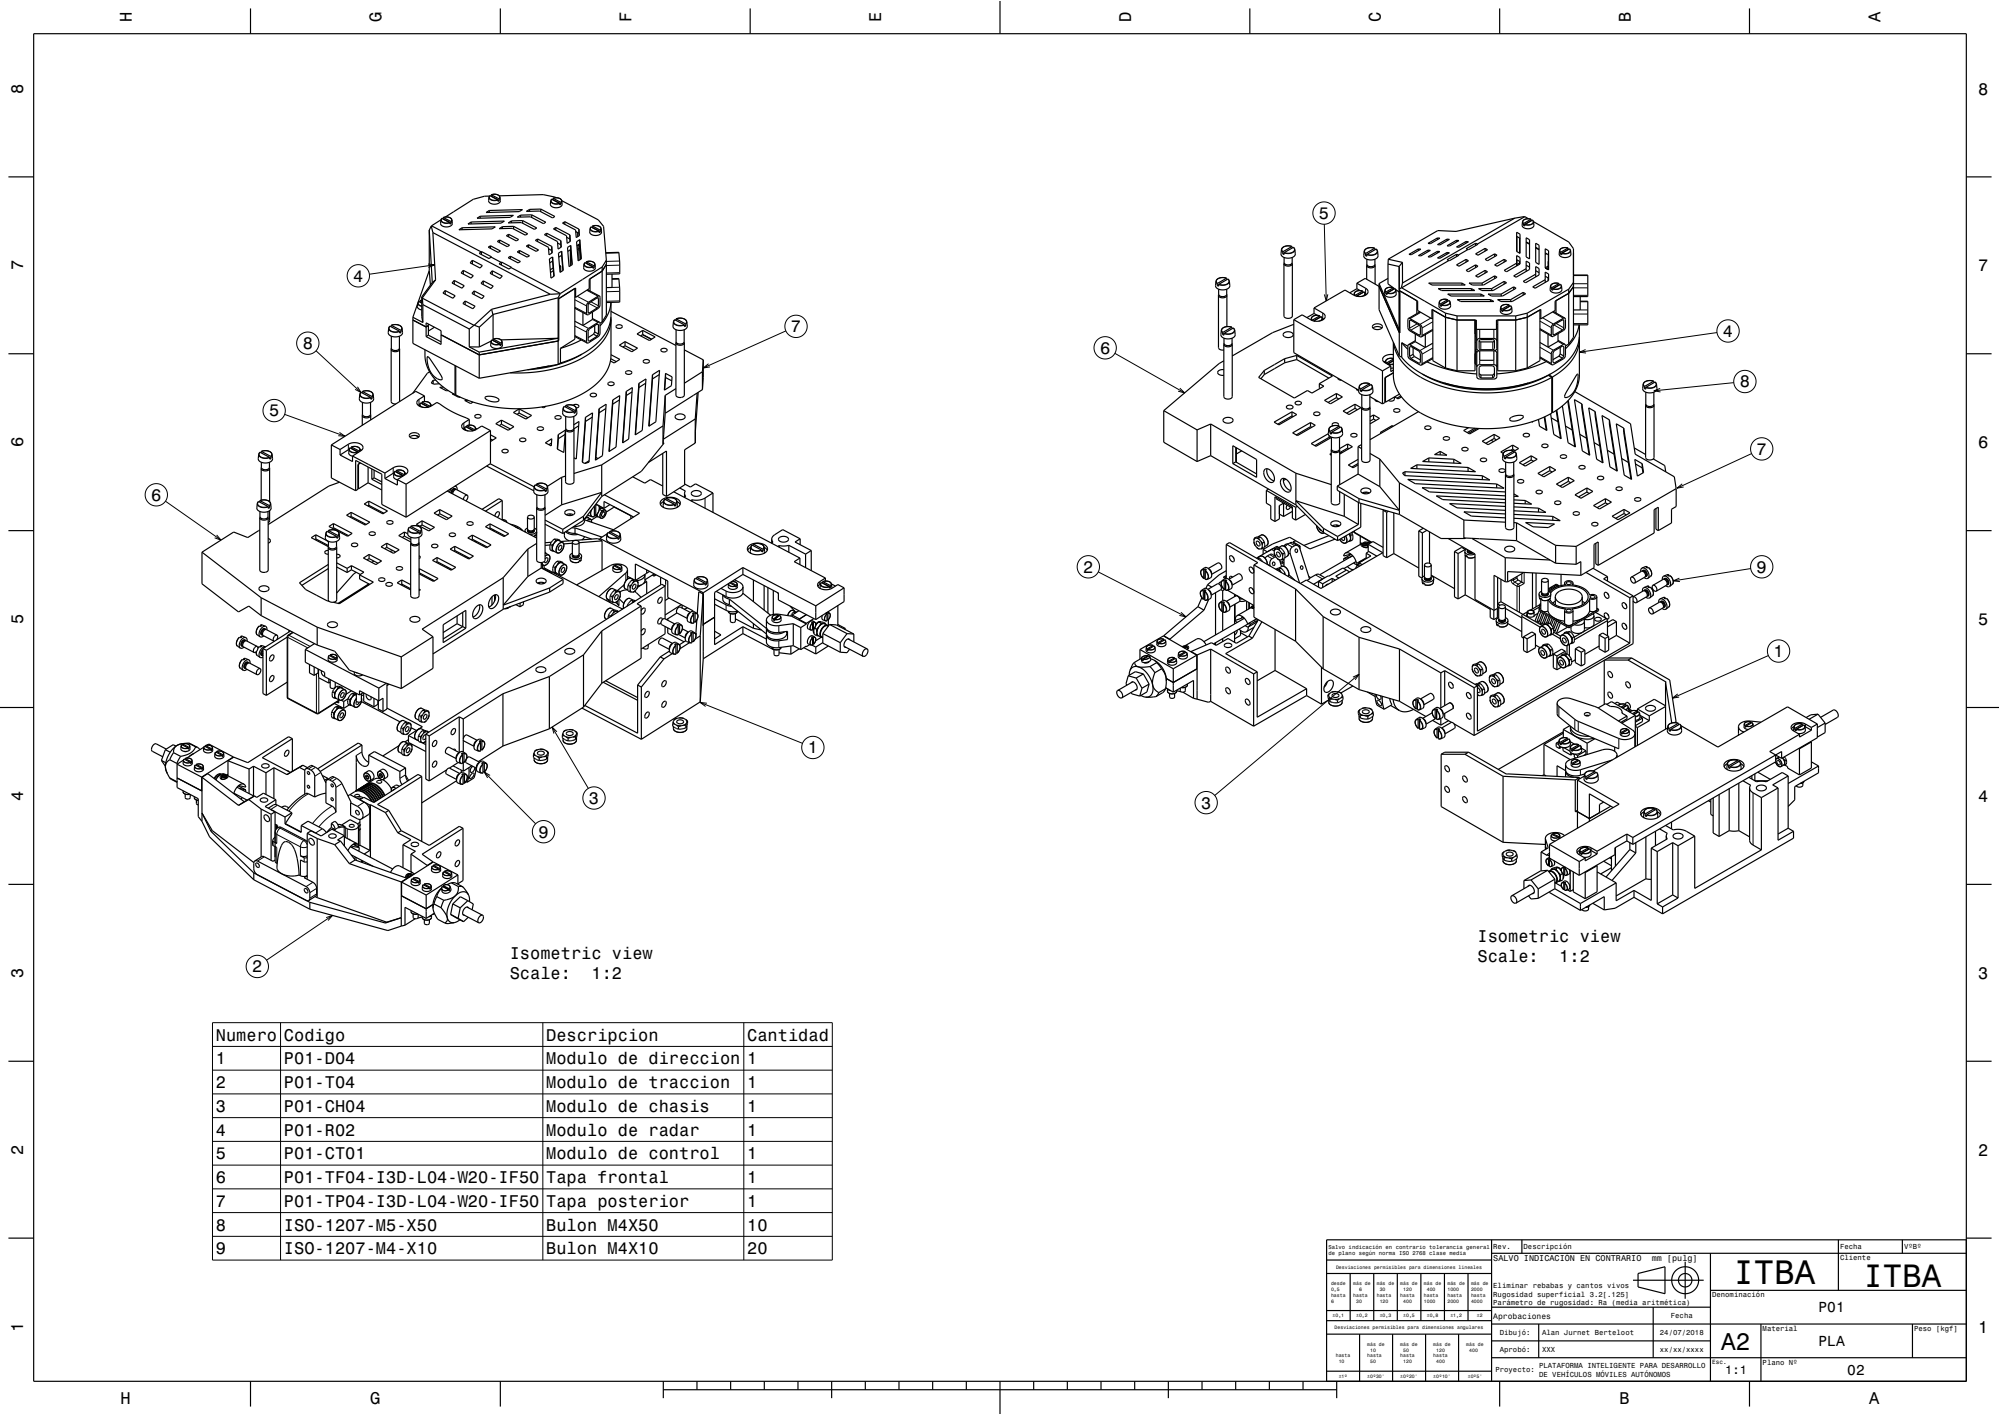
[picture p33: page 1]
Peso [kgf]; Plano Nº; más de; Isometric view Scale: 1:2; Numero Codigo; Descripcion; Cantidad; Modulo de direccion 1; Modulo de traccion 1; Modulo de chasis; Modulo de radar; Modulo de control; P01-TF04-I3D-L04-W20-IF50 Tapa frontal; P01-TP04-I3D-L04-W20-IF50 Tapa posterior; ISO-1207-M5-X50; Bulon M4X50; ISO-1207-M4-X10; Bulon M4X10

Salvo indicación en contrario tolerancia general
de plano según norma ISO 2768 clase media

Rev.
SALVO INDICACIÓN EN CONTRARIO mm [pulg]

Desviaciones permisibles para dimensiones lineales

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

Desviaciones permisibles para dimensiones angulares

Alan Jurnet Berteloot
XXX
PLATAFORMA INTELIGENTE PARA DESARROLLO
DE VEHÍCULOS MÓVILES AUTÓNOMOS

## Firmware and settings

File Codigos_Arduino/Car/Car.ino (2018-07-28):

#include <SPI.h>
#include <Wire.h>
#include <MemoryFree.h>
#include "rf_parser.h"
#include "servo_driver_lite.h"
#include "Brushless_driver.h"
#include "radar_definitions.h"
#include "I2C_parser.h"
#include "Math.h" 
#include "imu_driver_lite.h"


#define WHEEL_DIAMETER 80
#define AXIS_DISTANCE 0.34f
#define BATTERY_SENSOR_PIN A7
#define RF_TIMEOUT 1000 

servo_controller_lite* direccion;//(SERVO);
brushless_motor* motor;
mpu_9250_lite* imu_sensor;
rf_communication* rf24;//(1,SLAVE,9,10);
I2C_communication* radar_com;//(0,8,MASTER_I2C);
I2C_communication* control_com;//(0,8,MASTER_I2C);

typedef struct coordinates{
  float x;
  float y;
  float theta;
};

typedef struct frame{
  float x_pos;
  float y_pos;
  float theta;
  float velocity;
};

frame car; 
sensor_data sensor_measures;
controller_data control_orders;
float bateria;
bool activated_controller=false;

coordinates new_point;
bool brake=false;
imu_si_data imu_real_data;


void setup() {
  Serial.begin(250000);
  car.x_pos=0;
  car.y_pos=0;
  car.theta=0;
  

 
//  Serial.print("freeMemory()=");
//  Serial.println(freeMemory());

//  Serial.println("Configurando comunicacion RF"); 
  rf24= new rf_communication(1,SLAVE,9,10); 
//  Serial.print("freeMemory()=");
//  Serial.println(freeMemory());

  rf24->add_callback(set_motor_speed,SET_MOTOR_SPEED);
  rf24->add_callback(turn_steering,TURN_STEERING);
  rf24->add_callback(get_turns,GET_TURNS);
  rf24->add_callback(get_motor_speed,GET_MOTOR_SPEED);
  rf24->add_callback(get_battery_status,BATTERY_STATUS);
  rf24->add_callback(get_radar_measures,GET_RADAR_MEASURES);
  rf24->add_callback(set_turret_manual_mode,SET_TURRET_MANUAL_MODE);
  rf24->add_callback(set_turret_auto_mode,SET_TURRET_AUTO_MODE);
  rf24->add_callback(reset_controller,RESET_CONTROLLER);
  rf24->add_callback(set_new_x,SEND_CAR_NEW_X);
  rf24->add_callback(set_new_y,SEND_CAR_NEW_Y);
  rf24->add_callback(set_new_theta,SEND_CAR_NEW_THETA);
  rf24->add_callback(set_fil_x,SEND_CAR_X_FILTERED);
  rf24->add_callback(set_fil_y,SEND_CAR_Y_FILTERED);
  rf24->add_callback(set_fil_theta,SEND_CAR_THETA_FILTERED);
  rf24->add_callback(set_mode,CONTROL_MODE);
  rf24->add_callback(push_new_set_point,NEW_SET_POINT);
  
  rf24->add_callback(clear_goals,CLEAR_GOALS);
  rf24->add_callback(start_control,START_CONTROL);
  rf24->add_callback(stop_control,STOP_CONTROL);

  rf24->start();

//  Serial.println("Configurando direccion");
  direccion=new servo_controller_lite(SERVO);
//   Serial.print("freeMemory()=");
//    Serial.println(freeMemory());

  direccion->set_angle_limits(16,55,94);
  direccion->set_angle(0);
  
//  Serial.println("Configurando motor");
  motor=new brushless_motor();
//   Serial.print("freeMemory()=");
//    Serial.println(freeMemory());

  motor->setup(SPEEDSENSOR, []{motor->encoder_callback();}, RISING);
  motor->set_speed(0);

//  Serial.println("Configurando radar");
  radar_com= new I2C_communication(0,RADAR_ID,MASTER_I2C);
//   Serial.print("freeMemory()=");
//    Serial.println(freeMemory());

//  Serial.println("Configurando control");
  control_com= new I2C_communication(0,CONTROLLER_ID,MASTER_I2C);
//   Serial.print("freeMemory()=");
//    Serial.println(freeMemory());

 // Serial.println("Configurando imu");
  imu_sensor= new mpu_9250_lite();

  


  Serial.println("Listo.");
     Serial.print("freeMemory()=");
    Serial.println(freeMemory());

}


void loop() {
  static long last_update=0;
  // Leo el IMU
 // Serial.println("Leo IMU");
  imu_real_data=imu_sensor->get_imu_SI();
  
  //Actualizo posicion estimada del auto
//  Serial.println("Actualizo posicion");
  update_car_estimated_position();
  

  // Obtengo datos del controlador  
  //Serial.println("Obtengo datos del controlador");
  long now=millis();
  if (now-last_update>10){
    sensor_measures=radar_com->get_sensor_data(); 
    delay(5);
    control_com->send_car_data(SEND_CAR_DATA,sensor_measures,motor->read_speed(),car.theta,motor->get_turns(),direccion->get_angle());
    delay(5);
    control_orders=control_com->get_controller_data(); 
    last_update=now;
  }


  //Actualizo el controlador
  coordinates carpos;
  carpos.x=(float)car.x_pos;
  carpos.y=(float)car.y_pos;
  carpos.theta=car.theta;

  if (activated_controller){
    Serial.println(control_orders.speed);
    if( control_orders.speed>-500 && control_orders.speed< 500){
      motor->set_speed(control_orders.speed);
    }
    Serial.println(control_orders.steering);
    if(control_orders.steering>-50 && control_orders.steering< 50){
      direccion->set_angle(control_orders.steering);    
      set_turret_manual_mode(control_orders.turret_angle);
    }
  }


  // Actualizo el controlador del motor  
  //Serial.println("Actualizo controlador motor");
  motor->update_brushless();
  // Actualizo el manager de RF
  //Serial.println("Actualizo el manager de RF");

  rf24->update();  

  // Leo el estado de la bateria// Esto hay que modificarlo
  //Serial.println("Leo bateria");
  bateria=analogRead(BATTERY_SENSOR_PIN);
  bateria=bateria*10.0/1024;
}

void update_car_estimated_position(){
  static float last_turns=0;
  static long last_car_update=0;

  float turns=motor->get_turns();
  long now=millis();
  
  float deltaTime=(now-last_car_update)*1.0f/1000;
  car.velocity=motor->read_speed()*WHEEL_DIAMETER*0.10472/1000;
  if (activated_controller&&car.velocity>0){
    car.theta=car.theta+imu_real_data.gz*deltaTime;
  }

  if (last_turns!=turns){
    car.x_pos=turns*cos(car.theta*PI/180)*WHEEL_DIAMETER*PI;
    car.y_pos=turns*sin(car.theta*PI/180)*WHEEL_DIAMETER*PI;
    last_turns=turns;
  }

  last_car_update=millis();
  last_turns=turns;
}



////////////////////////////////////////////////////////// CALLBACKS DE RF ////////////////////////////////////////////////
void get_turns(float vueltas){
  double vueltas_eje=motor->get_turns();
  rf24->send_message(GET_TURNS,vueltas_eje);
}

void set_motor_speed(float speed){
  activated_controller=false;
  motor->set_speed(speed);
}

void get_battery_status(float data){
  rf24->send_message(BATTERY_STATUS,bateria);  
}

void get_motor_speed(float data){
  int  velocidad=motor->read_speed();
  rf24->send_message(GET_MOTOR_SPEED,velocidad);
}

void set_turret_manual_mode(float data){
  radar_com->send_message(RADAR_ID,SET_TURRET_MANUAL_MODE,data);
  Serial.print("Move radar to: ");
  Serial.println(data);
  
}

void set_turret_auto_mode(float data){
  radar_com->send_message(RADAR_ID,SET_TURRET_AUTO_MODE,data);
  Serial.print("Auto radar con agulo: ");
  Serial.println(data);
}


void turn_steering(float angle){
  activated_controller=false;
  direccion->set_angle(angle);
}
void set_new_x(float data){ 
  Serial.println("New X");
  control_com->send_message(CONTROLLER_ID,SEND_CAR_NEW_X,data);
}
void set_new_y(float data){
 control_com->send_message(CONTROLLER_ID,SEND_CAR_NEW_Y,data);
}
void set_new_theta(float data){
 control_com->send_message(CONTROLLER_ID,SEND_CAR_NEW_THETA,data);
}

void push_new_set_point(float data){
  control_com->send_message(CONTROLLER_ID,NEW_SET_POINT,0);
  //controller->set_new_point(new_point.x,new_point.y,new_point.theta  );
}

void reset_controller(float data){
  control_com->send_message(CONTROLLER_ID,RESET_CONTROLLER,0);
  motor->clear_turns();
  reset_car_data(1);
   activated_controller=false;
  Serial.println("Clear goals");
}
void clear_goals(float data){
  //controller->clean_points();
  control_com->send_message(CONTROLLER_ID,CLEAR_GOALS,0);
  
  Serial.println("Clear goals");
}
void start_control(float data){
  activated_controller=true;
//  controller->start_control();
  control_com->send_message(CONTROLLER_ID,START_CONTROL,0);
  Serial.println("Start controller");
}

void stop_control(float data){  
//  controller->stop_control();
control_com->send_message(CONTROLLER_ID,STOP_CONTROL,0);
Serial.println("Stop controller");
}



void set_fil_x(float data){
}
void set_fil_y(float data){
}
void set_fil_theta(float data){
}

void set_mode(float data){
}

void get_radar_measures(){
  rf24->send_car_data(sensor_measures,car.x_pos,car.y_pos,car.theta);
} 

void reset_car_data(float value){
  car.theta=0;
  car.x_pos=0;
  car.y_pos=0;
}

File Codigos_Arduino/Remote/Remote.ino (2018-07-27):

#include <SPI.h>
#include "CComands.h"
#include "rf_parser.h"

#include "serialParser.h"


#define XAXIS A2
#define YAXIS A1
#define SWITCH 2

serialManager *manager_serial;
rf_communication *rf24;
long lastdatatime;
car_data real_data;
bool remote_control=false;
bool connected_rf=false;

void setup() {
  // put your setup code here, to run once:
  Serial.begin(250000);

  manager_serial = new serialManager();
 Serial.println("New rfManager");
  rf24=new rf_communication(0,MASTER,9,10);
  rf24->add_callback(show_turns,GET_TURNS);
  rf24->add_callback(show_motor_speed,GET_MOTOR_SPEED);
  rf24->add_callback(show_battery_status,BATTERY_STATUS);
  rf24->add_car_data_callback(get_car_data);
  rf24->add_callback(set_turret_manual_mode,SET_TURRET_MANUAL_MODE);
  rf24->add_callback(set_turret_auto_mode,SET_TURRET_AUTO_MODE);
  rf24->add_callback(reset_controller,RESET_CONTROLLER);
 
  Serial.println("Starting rfManager");
  rf24->start();

  manager_serial->add_callback(set_motor_speed,SET_MOTOR_SPEED);
  manager_serial->add_callback(turn_steering,TURN_STEERING);
  manager_serial->add_callback(get_motor_speed,GET_MOTOR_SPEED);
  manager_serial->add_callback(get_turns,GET_TURNS);
  manager_serial->add_callback(get_battery_status,BATTERY_STATUS);
  manager_serial->add_callback(set_turret_manual_mode,SET_TURRET_MANUAL_MODE);
  manager_serial->add_callback(set_turret_auto_mode,SET_TURRET_AUTO_MODE);
  manager_serial->add_callback(get_radar_measures,GET_RADAR_MEASURES);
  manager_serial->add_callback(reset_controller,RESET_CONTROLLER);

  //settings
  manager_serial->add_callback(send_new_x,SEND_CAR_NEW_X);
  manager_serial->add_callback(send_new_y,SEND_CAR_NEW_Y);
  manager_serial->add_callback(send_new_theta,SEND_CAR_NEW_THETA);
  manager_serial->add_callback(send_fil_x,SEND_CAR_X_FILTERED);
  manager_serial->add_callback(send_fil_y,SEND_CAR_Y_FILTERED);
  manager_serial->add_callback(send_fil_theta,SEND_CAR_THETA_FILTERED);
  manager_serial->add_callback(control_mode,CONTROL_MODE);
  manager_serial->add_callback(show_car_data,SHOW_ALL_DATA);

  manager_serial->add_callback(push_new_set_point,NEW_SET_POINT);
  manager_serial->add_callback(clear_goals,CLEAR_GOALS);
  manager_serial->add_callback(start_control,START_CONTROL);
  manager_serial->add_callback(stop_control,STOP_CONTROL);


  lastdatatime=millis();
  Serial.println("Ready");  
  pinMode(XAXIS,INPUT);
  pinMode(YAXIS,INPUT);
  pinMode(SWITCH,INPUT);
  digitalWrite(SWITCH, HIGH);
  attachInterrupt(digitalPinToInterrupt(SWITCH),change_control_mode,RISING );
}

void change_control_mode(){
  
  static long last_change=0;
  long now=millis();
  if(now-last_change>1000){    
  if (remote_control){
      remote_control=false;
      Serial.println("Control automatico.");
    }else{
      remote_control=true;
      Serial.println("Control manual.");
    }
    last_change=now;
  }
  
}

void loop() {
  // put your main code here, to run repeatedly:
  manager_serial->update();
  rf24->update();
  long now=millis();
  if (now-lastdatatime>50){
 //   Serial.println("get_radar");
    
    lastdatatime=now;
    if (remote_control){
      int set_speed=-((analogRead(YAXIS)-1024.0/2)*200.0*2/1024);
      int set_angle=-((analogRead(XAXIS)-1024.0/2)*50.0*2/1024);
      Serial.println(set_speed);
      Serial.println(set_angle);
      set_motor_speed(set_speed);
      turn_steering(set_angle);
    }else{
      get_radar_measures(1);
    }
  }

  
}


void push_new_set_point(float data){
  Serial.println("Pushing new point");
  
  rf24->send_message(NEW_SET_POINT,data);
  Serial.println("Ready");  
}
void clear_goals(float data){
  Serial.println("Clear_goals");
  
  rf24->send_message(CLEAR_GOALS,data);
  Serial.println("Ready");  
}
void start_control(float data){
  Serial.println("start_control");   
  rf24->send_message(START_CONTROL,data);
  Serial.println("Ready"); 
}
void stop_control(float data){
  Serial.println("stop_control");
  rf24->send_message(STOP_CONTROL,data);
  Serial.println("Ready");  
}

void send_new_x(float data){
  Serial.print("Setear new x: ");
  Serial.print(data);
  Serial.println(" m");  
  
  rf24->send_message(SEND_CAR_NEW_X,data);
  Serial.println("Ready");  
}

void send_new_y(float data){
  Serial.print("Setear new y: ");
  Serial.print(data);
  Serial.println(" m");  
  
  rf24->send_message(SEND_CAR_NEW_Y,data);
  Serial.println("Ready");  
}

void send_new_theta(float data){
  //Serial.print("Setear new theta: ");
  //Serial.print(data);
  //Serial.println(" m");   
  rf24->send_message(SEND_CAR_NEW_THETA,data);
}


void send_fil_x(float data){
  //Serial.print("Setear filtered x: ");
  //Serial.print(data);
  //Serial.println(" m");  
  rf24->send_message(SEND_CAR_X_FILTERED,data);
}

void send_fil_y(float data){
  //Serial.print("Setear filtered y: ");
  //Serial.print(data);
  //Serial.println(" m");    
  rf24->send_message(SEND_CAR_Y_FILTERED,data);
}

void send_fil_theta(float data){
  //Serial.print("Setear filtered theta: ");
  //Serial.print(data);
  //Serial.println(" grads");   
  rf24->send_message(SEND_CAR_THETA_FILTERED,data);
}
void control_mode(float data){
  //Serial.print("Setear modo de control: ");
  //Serial.print(data);
    //Serial.println(" n modo"); 
  rf24->send_message(CONTROL_MODE,data);
}


void set_motor_speed(float speed){
  //Serial.print("Sending speed");
  //Serial.println(speed);
  rf24->send_message(SET_MOTOR_SPEED,speed);
  
}

void turn_steering(float angle){
  rf24->send_message(TURN_STEERING,angle);
}

void get_turns(float data){
  rf24->send_message(GET_TURNS,data);
}

void get_motor_speed(float data){
  rf24->send_message(GET_MOTOR_SPEED,data);
}

void get_battery_status(float data){
  rf24->send_message(BATTERY_STATUS,data);
}

void set_turret_manual_mode(float data){
  //Serial.print("Moviendo torre a: ");
  //Serial.println(data);
  rf24->send_message(SET_TURRET_MANUAL_MODE,data);
}
void reset_controller(float data){
  //Serial.println("Reseteando datos");
  rf24->send_message(RESET_CONTROLLER,data);
  Serial.println("Ready");  
}

void set_turret_auto_mode(float data){
 
 rf24->send_message(SET_TURRET_AUTO_MODE,data);
}


void show_turns(float data){
  /*Serial.print("Vueltas: ");
  Serial.println(data);*/
}

void show_motor_speed(float data){
  /*Serial.print("Velocidad: ");
  Serial.print(data);
  Serial.println(" RPM");*/
}

void show_battery_status(float data){
 /* Serial.print("Bateria: ");
  Serial.print(data);
  Serial.println(" V");*/
}

void get_radar_measures(float data){
  rf24->send_message(GET_RADAR_MEASURES,data);
  
}
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

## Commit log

2018-07-25 Actualizacion
    Version 1.0
    [IS0_10511_M3_STEEL_PREVAILING_TORQUE_TYPE_HEXAGON_THIN_NUT.CATPart, IS0_10511_M4_STEEL_PREVAILING_TORQUE_TYPE_HEXAGON_THIN_NUT.CATPart, IS0_10511_M5_STEEL_PREV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]
2018-07-25 Correccion de piezas editables
    [P01-D04.CATProduct, P01-R02.CATProduct, P01-T04.CATProduct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]
2018-07-25 Agrego ruedas
    [IS0_10511_M5_STEEL_PREVAILING_TORQUE_TYPE_HEXAGON_THIN_NUT_2.CATPart, IS0_10511_M5_STEEL_PREVAILING_TORQUE_TYPE_HEXAGON_THIN_NUT_New_118_2.CATPart, IS0_10511_M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]
2018-07-25 Cambios menores
    [Partes_auto.csv, Partes_radar.csv, Partes_traccion.csv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]
2018-07-26 Pasos de ensamble
